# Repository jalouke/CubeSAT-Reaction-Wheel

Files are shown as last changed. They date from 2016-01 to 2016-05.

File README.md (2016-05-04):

# CubeSAT-Reaction-Wheel

Portland State University is developing Oregon’s first orbital satellite, a 2U Cubesat dubbed Oresat. This cubesat will use a reaction wheel system for attitude control and pointing of the onboard antennas and cameras. I am developing the controller, designing the structure and sourcing hardware for both the space rated system and a ground test system that will also be used for demonstration purposes. This system has been tested using the Dryden Drop Tower at PSU as well as in captive hanging tests. The current controller is a simple proportional controller, however using data collected from the drop test I will refine the model and implement a more sophisticated controller. Video of the tests can be seen at:  [Captive Controller Hanging Test](https://www.youtube.com/watch?v=Is1gPHlewtgand) and [Dryden Drop Tower Micro-Gravity Test](https://www.youtube.com/watch?v=cC2FpmCP5B4)

Both of the previous tests were conducted using a simple open loop proportional controller that was tuned via test to induce a slightly underdamped response. This was to create data that can be more easily compared to an ideal model.

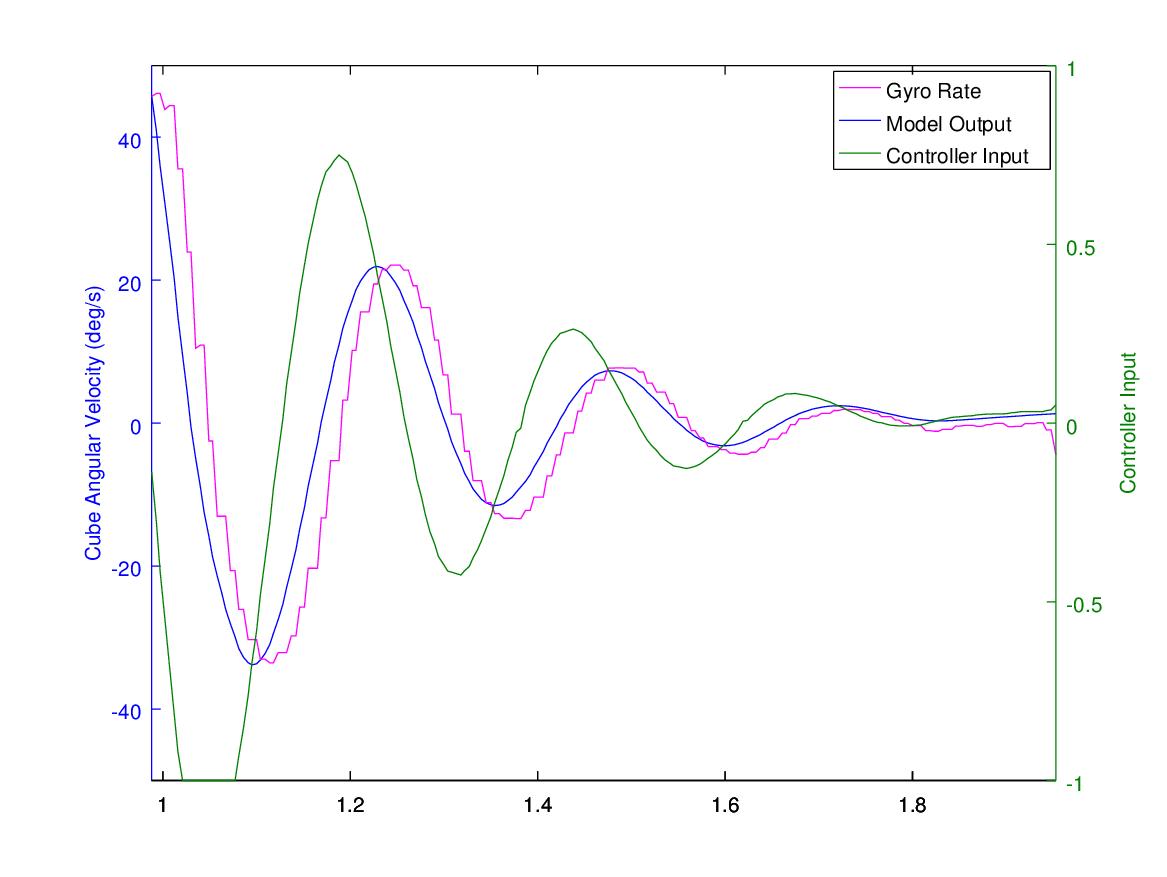
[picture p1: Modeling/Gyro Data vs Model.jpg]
CubeSat Model Comparison


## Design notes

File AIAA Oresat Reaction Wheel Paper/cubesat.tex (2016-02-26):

% `template.tex', a bare-bones example employing the AIAA class.
%
% For a more advanced example that makes use of several third-party
% LaTeX packages, see `advanced_example.tex', but please read the
% Known Problems section of the users manual first.
%
% Typical processing for PostScript (PS) output:
%
%  latex template
%  latex template   (repeat as needed to resolve references)
%
%  xdvi template    (onscreen draft display)
%  dvips template   (postscript)
%  gv template.ps   (onscreen display)
%  lpr template.ps  (hardcopy)
%
% With the above, only Encapsulated PostScript (EPS) images can be used.
%
% Typical processing for Portable Document Format (PDF) output:
%
%  pdflatex template
%  pdflatex template      (repeat as needed to resolve references)
%
%  acroread template.pdf  (onscreen display)
%
% If you have EPS figures, you will need to use the epstopdf script
% to convert them to PDF because PDF is a limmited subset of EPS.
% pdflatex accepts a variety of other image formats such as JPG, TIF,
% PNG, and so forth -- check the documentation for your version.
%
% If you do *not* specify suffixes when using the graphicx package's
% \includegraphics command, latex and pdflatex will automatically select
% the appropriate figure format from those available.  This allows you
% to produce PS and PDF output from the same LaTeX source file.
%
% To generate a large format (e.g., 11"x17") PostScript copy for editing
% purposes, use
%
%  dvips -x 1467 -O -0.65in,0.85in -t tabloid template
%
% For further details and support, read the Users Manual, aiaa.pdf.

% Try to reduce the number of latex support calls from people who
% don't read the included documentation.
%
\typeout{}\typeout{If latex fails to find aiaa-tc, read the README file!}
%

\documentclass[]{aiaa-tc}% insert '[draft]' option to show overfull boxes
\usepackage{amssymb}
\usepackage{amsmath} 

 \title{An Open-Source Reaction Wheel System for Oregon's First Satellite}

 \author{
  Jeremy A. Louke\\
  {\normalsize\itshape
   Portland State Aerospace Society, Portland, OR, 97201}\\
  \and
  Erin S. Schmidt\\
  {\normalsize\itshape
  Portland State University, Portland, OR, 97201}
 }

 % Data used by 'handcarry' option if invoked
 \AIAApapernumber{YEAR-NUMBER}
 \AIAAconference{Conference Name, Date, and Location}
 \AIAAcopyright{\AIAAcopyrightD{YEAR}}

 % Define commands to assure consistent treatment throughout document
 \newcommand{\eqnref}[1]{(\ref{#1})}
 \newcommand{\class}[1]{\texttt{#1}}
 \newcommand{\package}[1]{\texttt{#1}}
 \newcommand{\file}[1]{\texttt{#1}}
 \newcommand{\BibTeX}{\textsc{Bib}\TeX}

\begin{document}

\maketitle

\begin{abstract}
Portland State University is developing Oregon's first orbital satellite, a 2U Cubesat, dubbed Oresat. This cubesat will use a reaction wheel system for attitude control and pointing of the onboard low-gain antenna. Details of the current stage of development of the reaction wheel ground test article, and its controller, are presented here. Future work includes attitude control testing in the brief (2.1 s) free-fall environment of Portland State University's Dryden Drop Tower.
\end{abstract}

\section*{Nomenclature}

\begin{tabbing}
  XXX \= \kill% this line sets tab stop
  $M_0^{+ \circlearrowleft}$ \qquad Moment in the x-axis (N m)\\
  $T^0$ \qquad Torque (N m)\\
  $\theta$ \qquad Angular position (${}^{\circ}$)\\
  $\dot{\theta}$ \qquad Angular velocity(${}^{\circ}/s$)\\ 
  $\ddot{\theta}$ \qquad Angular velocity(${}^{\circ}/s^2$) \\
  $I$ \qquad Moment of Inertia (N $\textrm{m}^2$)\\
  $b$ \qquad Damping Coefficient (N s/m)\\ 
  $G$ \qquad Spring Coefficient (N/m)\\ \\
  \textit{Subscripts}\\
  $x$ \qquad Index for Cartesian axes \\
  $rw$\qquad Reaction Wheel\\
  $n$ \qquad Motor Index\\
  $A, B, C, D$ \qquad Indices for Motors A, B, C, and D\\
 \end{tabbing}

\section{Introduction}
Small educational satellites have been launched by dozens of universities around the United States as part of NASA’s CubeSat Launch Initiative, especially under the auspices of the Educational Launch of Nanosatellites (ELaNa) program. As of 2015 cubesats from 29 states have flown under the program, however the great state of Oregon has yet to join their ranks\cite{Mahoney:15bk}. During the summer of 2015 the Oresat project was initiated by the Portland State Aerospace Society to rectify this situation. The Portland State Aerospace Society (PSAS) is an engineering student organization and citizen science project located at Portland State University dedicated to developing low-cost, open-source, and open-hardware high-powered rockets and avionics systems with special interests in venture class launch vehicle technologies and nanosatellites\cite{PSAS:15bk}.\\

The Oresat satellite will be a Cal Poly design-specification 2U cubesat\cite{Cubesat:14bk}. Oresat is pictured in Figure \ref{fig:oresat}. The project objectives are to test several subsystems in the environment of a 400 km circular Low Earth Orbit, including PSAS’s Sputnik board, and DxWiFi subsystems. The Sputnik command, control, and communication (C3) board is based on a MKW01Z128 microcontroller, and has a custom “arduino-like” breakout. Sputnik is being designed expressly for the space environment, and will include some measure of fault-tolerance and radiation hardening. Another major project, dubbed DxWiFi, is to be able to communicate space-to-ground, and ground-to-space via a COTS IEEE 802.11b radio module aboard the cubesat. Ground stations for cubesat telemetry downlink are expected to be part of the SatNOGs open-source satellite ground station network. Due to practical issues with telemetry downlink power budgets and and the limitations of the low-gain deployable antenna some element of directional pointing is required. Following from this is the need for a robust system to provide attitude control for Oresat attitude control system. PSAS has selected a reaction wheel based system to provide attitude control for Oresat. Per PSAS’s open-source mandate all  (non-ITAR) project development deliverables are being made publicly available under a GNU GPL v2 license\cite{Oresat:15bk}. It is hoped by the authors, and the members of PSAS that the discourse around educational cubesats and their design will be elevated by making the information for this project publicly available.

\begin{figure}[h!]
  \centering
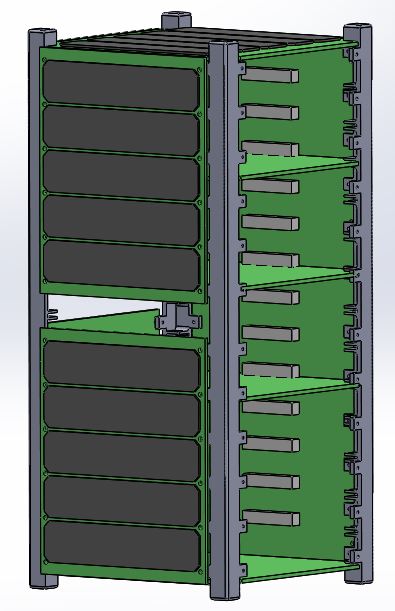
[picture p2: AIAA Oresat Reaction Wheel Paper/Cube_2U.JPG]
  
  \caption{Speculative mockup in SolidWorks of the Oresat chassis.}
  \label{fig:oresat}
\end{figure}

\section{Concept Definition}
	Angular rate and pointing precision requirements for the flight attitude control system are determined from orbital parameters (likely those offered by Nanoracks deployment from the ISS) and the expected performance of the PSAS DxWiFi telemetry system. The ground test article is a proof of concept and uses inexpensive COTS DC brushless motors which are significantly more powerful than those required for the flight use case. The ground test article is broadly similar in design to the flight system, for example by using 4 momentum-wheels in a pyramid configuration for added redundancy and on-orbit mission assurance. Such a design is similar one recently developed for a master's thesis project at California Polytechnic State University San Luis Obispo\cite{Logan:08bk}. A magnetorquer is used to periodically dump accumulated momentum into the Earth's magnetic field. The principle difference between the ground test and flight designs is that the ground test article uses the 1U form factor whereas Oresat will be 2U.

\section{Design and Fabrication}
	The Oresat reaction wheel system chassis was developed using rapid prototyping techniques over a short time period. This enables rapid design iteration cycles. A mockup 1U cubesat structure was drafted in SolidWorks CAD, and fabricated by FDM 3D printers. The cubesat structural rails were printed with recesses for hex nuts to ease assembly. The ground test article is shown in Figure \ref{fig:rcs} As previously noted there are several departures in the design of the ground test article from the flight system. Among these are COTS DC brushless motors used to drive the momentum wheels. Having a very high RPM limit, specifically 22,000 RPM, these motors provide substantially more torque, shaft power, and shaft speed than required by the flight system. The use of such motors is justified due to the need to counter 1-g gravity in benchtop tests, to react quickly to perturbations, and to test the limits of the controller rise time. Additionally, the ground test article is not constrained by requirements for power consumption as the flight system surely will be. 

\begin{figure}[h!]
  \centering
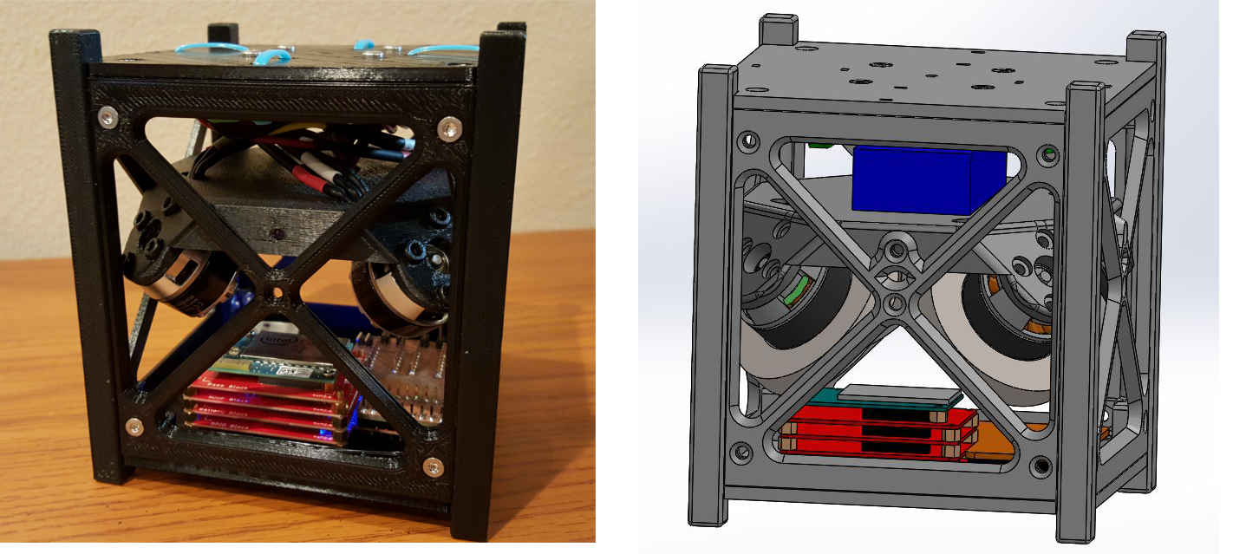
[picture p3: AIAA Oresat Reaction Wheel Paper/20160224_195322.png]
  
  \caption{Reaction wheel ground test articles, completed prototype and CAD design in SolidWorks.}
  \label{fig:rcs}
\end{figure}

\section{Controls Simulation and Design}
The Controller is implemented on an Intel Edison with code written in Python. The Edison receives feedback from a 9-DoF IMU and sends signals via GPIO to the motors. The top-level controller design procedure was as follows:
\begin{enumerate}
\item Determine the transfer functions from dynamics analysis of free body diagrams of the system
\item Create simulation in GNU Octave
\item Design the controller using classical Bode techniques
\end{enumerate}
The transfer functions are determined with a dynamics analysis of the free body diagram, shown schematically for a single axis in Figure \ref{fig:FBD}. The forces acting on the cube are the torques created by the motors $T_i^0$, damping effects $b_1 \dot{\theta}_{cube}$, and spring effects $G_1 \theta_{cube}$. Summing the moments around the center of gravity gives the following equation:\\

\begin{equation}
\label{eq:moment}
\sum M_0^{+ \circlearrowleft} = I_{x,cube} \ddot{\theta}_{x,cube} = T^0_{Ax} + T^0_{Bx} - T^0_{Cx} - T^0_{Dx} + T^0_x - \dot{\theta}_{x,cube} - G_x \theta_{x,cube}
\end{equation}\\
	
Solving Eqn. \ref{eq:moment} so that $\theta_{cube}$ and its derivatives are on the left side, and the motor torques are on the right side, as well as setting the system to Standard Equilibrium Position (at SEP the input perturbations are set to zero) and substituting the torque-inertia relation:\\

\[
T^0_x = 0
\]
\[
T^0_{nx} = I_{rw}\ddot{\theta}_n\]\\

This gives us the following equation:\\
 
\[
I_{x,cube} \alpha_x + b_x \dot{\theta}_{x,cube} + G_x \theta_{x,cube} = \sin(45^{\circ}) I_{rw} (\ddot{\theta}_A + \ddot{\theta}_B -\ddot{\theta}_C - \ddot{\theta}_D)
\]\\	
The definition of a transfer function is the output of a system with respect to a single input, so all motors are set to zero except for one (A for this example) and apply a Laplace transform to the equation:\\

\[
\frac{I_{x,cube}}{\sin(45^{\circ}) I_{rw}} \theta_{x,cube} s^2 +
\frac{b_x}{\sin(45^{\circ}) I_{rw}} \theta_{x,cube} s +
\frac{G_x}{\sin(45^{\circ}) I_{rw}} \theta_{x,cube} = \theta_A s^2
\]\\
	
Finally moving $\theta_{cube}$ and $\theta_A$ to the left side of the equation and everything else to the right, gives us a transfer function:\\

\begin{equation}
\label{eq:xfer}
G_A(s)=\frac{\theta_{x,cube}(s)}{\theta_A(s)}=\frac{s^2}{\cfrac{I_{x,cube}}{\sin(45^{\circ}) I_{rw}}s^2 + \cfrac{b_x}{\sin(45^{\circ}) I_{rw}}s + \cfrac{G_x}{\sin(45^{\circ}) I_{rw}}}
\end{equation}\\
	
Using the transfer functions, given schematically for one axis by Eqn. \ref{eq:xfer} a simulation was created in GNU Octave which yielded step response plots shown in Figure \ref{fig:simulation}. The simulation will further aid in Bode analysis for the determination of stability margins. These relate the frequency response of the system to its time response. The Margins can be adjusted with the use of a controller to affect the time response characteristics of the system. In the case of the ground test system the rise time for a $90^{\circ}$ step input should be under 1 second. 
\begin{figure}[h!]
  \centering
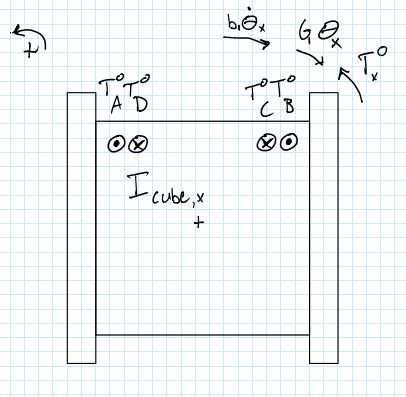
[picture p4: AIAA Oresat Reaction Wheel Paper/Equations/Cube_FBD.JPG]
  
  \caption{Free Body Diagram of the cubesat in the Cartesian X axis.}
  \label{fig:FBD}
\end{figure}

\begin{figure}[h!]
  \centering
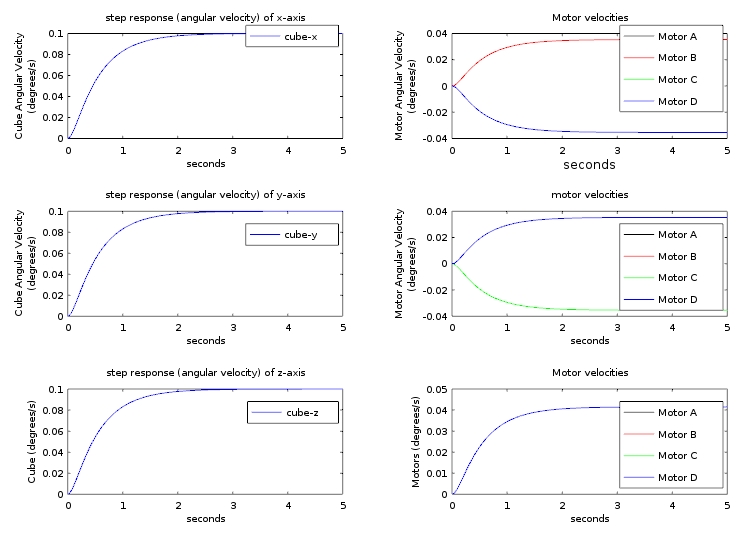
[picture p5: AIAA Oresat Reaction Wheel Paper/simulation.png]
  
  \caption{Angular velocity step responses in the cardinal axes of the CubeSat (left side), and individual motor velocities (right side).}
  \label{fig:simulation}
\end{figure}
\section{Future work}
An exciting testing opportunity involves exploiting the high-quality $\mu$-gravity environment of Portland State University's Dryden Drop Tower (DDT) facility for free fall tests of the reaction wheel system. The Dryden Drop Tower, patterned on the 2.2 Second Drop Tower facility at NASA's Glenn Research Center in Cleveland, Ohio, is optimized for exceptionally fast drop turnaround times. The DDT is one of the most productive Drop Towers in the world for its class, with more than xx drops over its xx year history. The DDT's 2.1 seconds of free-fall conditions provide unique opportunities for the observation of phenomena that are usually masked at the macro-scale in 1-g gravity fields. In the planned experiment the reaction wheel system will be commanded to complete two independent $90^{\circ}$ roll programs of the cubesat in the brief cinderella-like moment before the simulacrum of $\mu$-gravity disappears 2.1 seconds later.

It is expected that the 1-g and $\mu$-gravity testing campaigns for the Oresat reaction wheel system will be completed by early June. This should leave a substantial allowance of time for further design iterations leading up to the Oresat Critical Design Review before the next round of ELaNa proposals are due in November 2016.

\begin{thebibliography}{9}% maximum number of references (for label width)

\bibitem{Mahoney:15bk}
Mahoney, Erin. {\it CubeSat Launch Initiative: 50 CubeSats from 50 States in 5 Years.} NASA, April 9, 2015. http://www.nasa.gov/content/cubesat-launch-initiative-50-cubesats-from-50-states-in-5-years.\\

\bibitem{PSAS:15bk}
{\it Portland State Aerospace.} PSAS. Accessed February 25, 2016. http://psas.pdx.edu.\\

\bibitem{Cubesat:14bk}
The CubeSat Program, {\it Cal Poly SLO. CubeSat Design Specification Rev. 13.} San Luis
Obispo: California Polytechnic State University; 2014.\\

\bibitem{Oresat:15bk}
{\it Oregon Small Satellite Project.} GitHub. Accessed February 25, 2016. https://github.com/oresat.\\

\bibitem{Logan:08bk}
Logan, Jeffery. {\it Control and Sensor Development on a Four-Wheel Pyramidal Reaction Wheel Platform,} Master’s Thesis, California Polytechnic State University, San Luis Obispo, 2008.\\

\end{thebibliography}

\end{document}

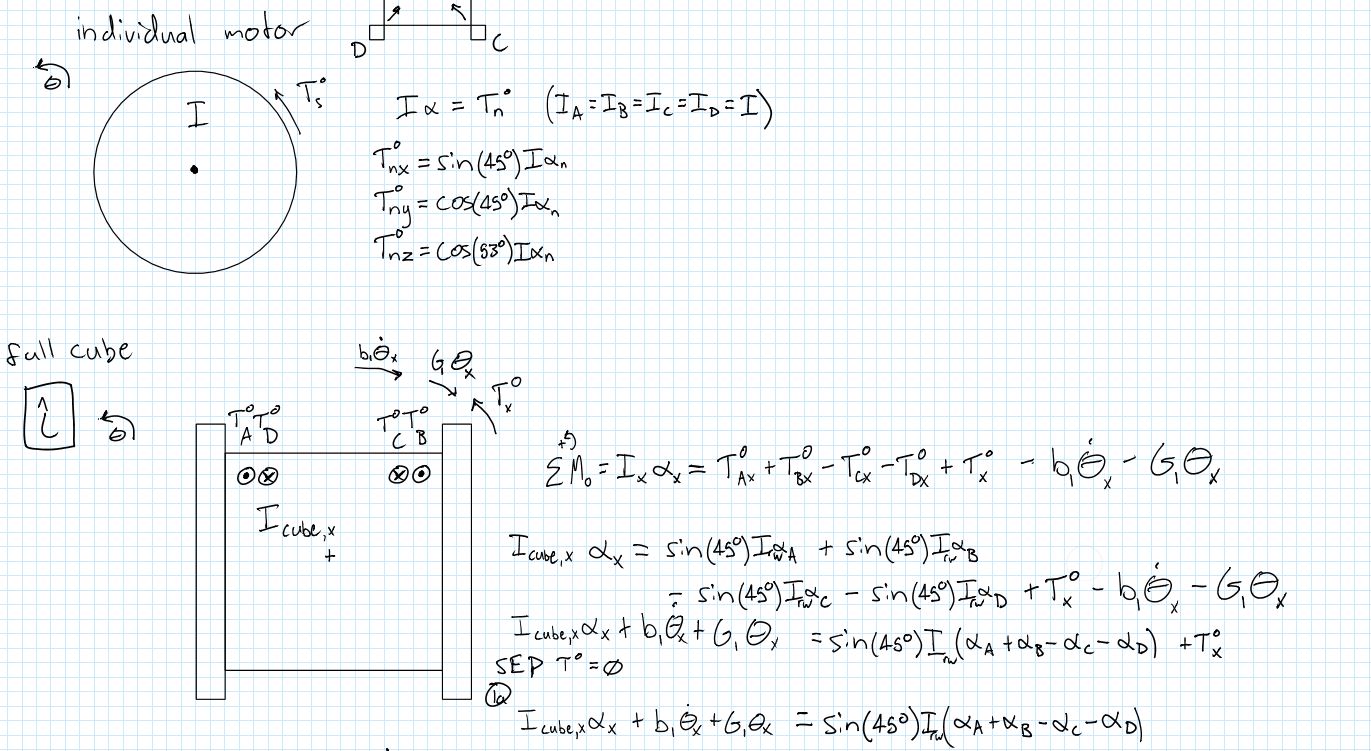
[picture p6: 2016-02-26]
AIAA Oresat Reaction Wheel Paper/Equations/Moment Sum and equation 1_a.JPG

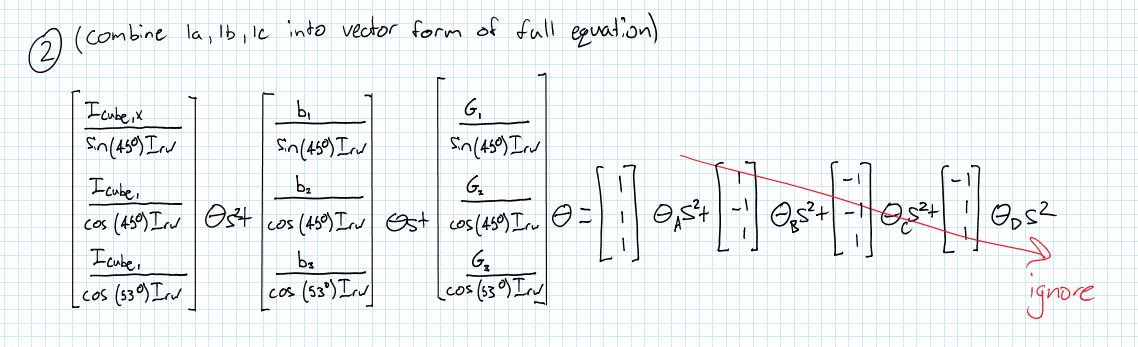
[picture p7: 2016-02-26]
AIAA Oresat Reaction Wheel Paper/Equations/Equation 2.JPG

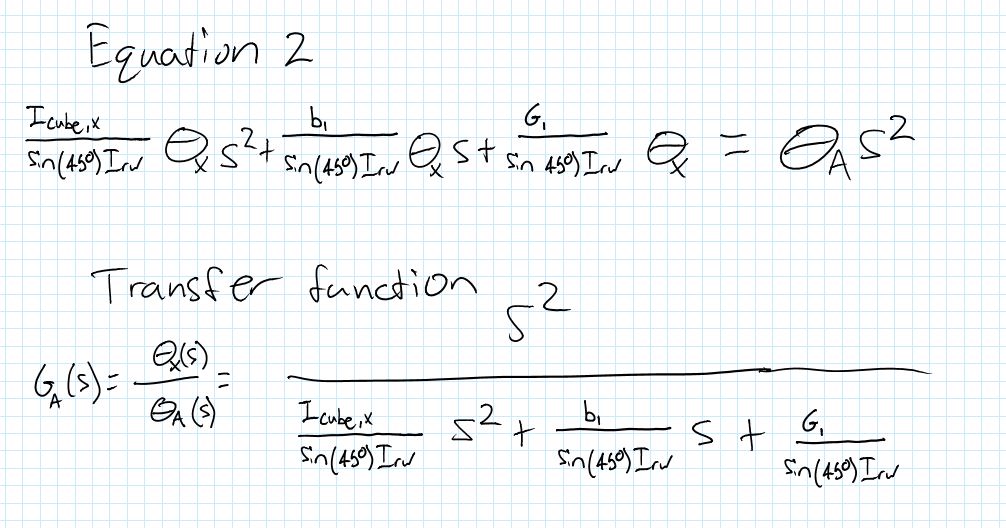
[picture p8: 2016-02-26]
AIAA Oresat Reaction Wheel Paper/Equations/CubeSat Transfer function and Equation 2.JPG

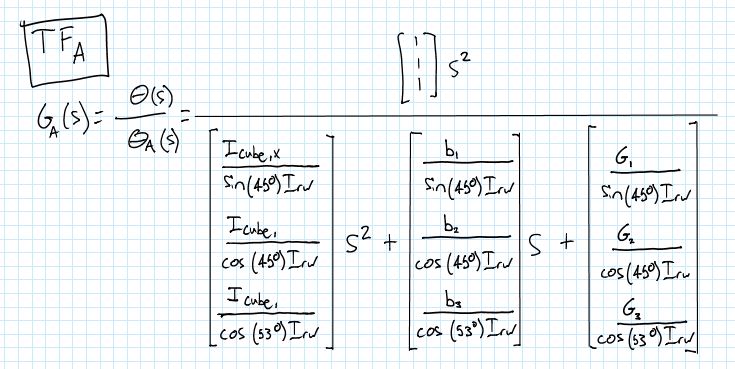
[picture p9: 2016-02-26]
AIAA Oresat Reaction Wheel Paper/Equations/Transfer Function.JPG

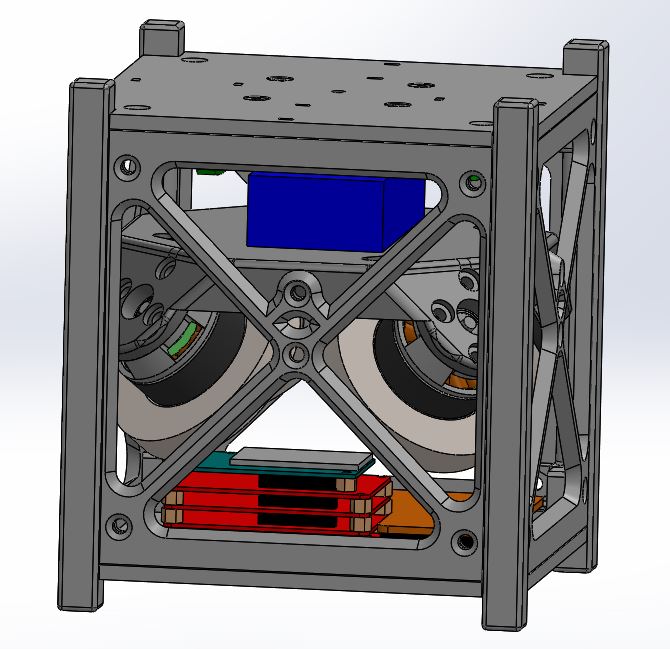
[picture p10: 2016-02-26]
AIAA Oresat Reaction Wheel Paper/Cube_RW_Full.JPG

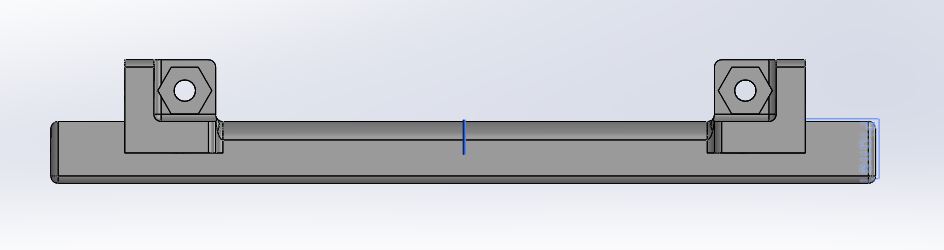
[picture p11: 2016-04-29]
SW_CAD_1U_cubesat/New STL/Corner rail.JPG

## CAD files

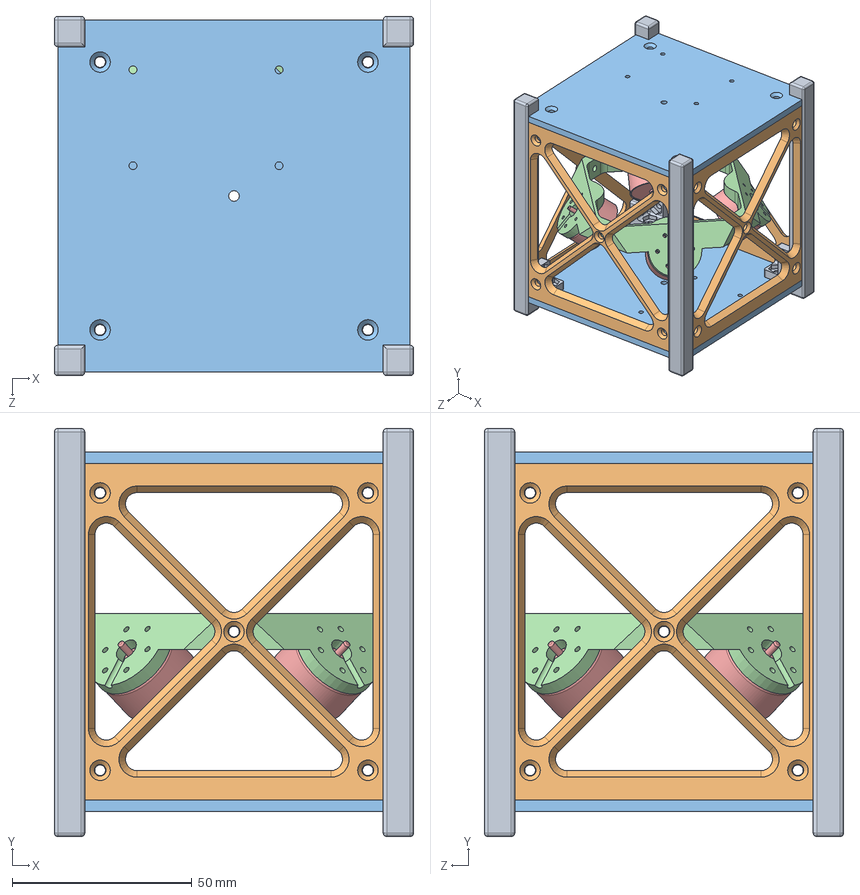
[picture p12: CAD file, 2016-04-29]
SW_CAD_1U_cubesat/V1/Cube sat assembly.SLDASM
100.0 x 113.5 x 100.0 mm
Corner rail x 4
Sides x 4
Z side x 2
reaction wheel mount
reaction wheel motor x 4

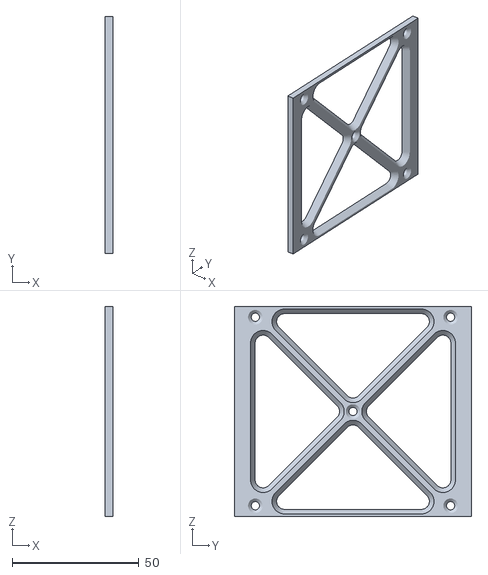
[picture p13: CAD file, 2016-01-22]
SW_CAD_1U_cubesat/V1/STL/Cube sat assembly - Sides-2.STL
3.17 x 93.6 x 83.0

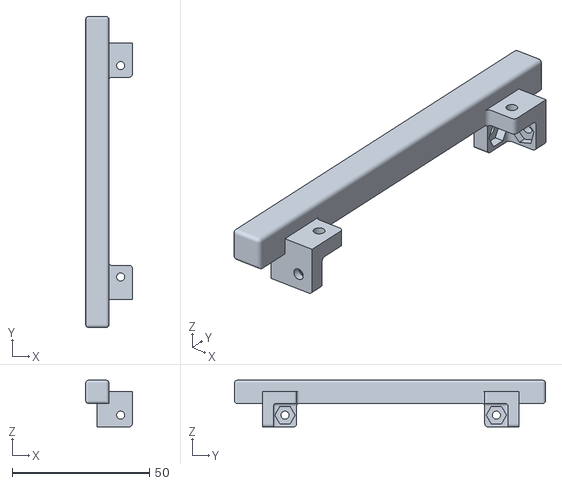
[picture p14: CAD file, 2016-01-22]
SW_CAD_1U_cubesat/V1/STL/Cube sat assembly - Corner rail-4.STL
17.0 x 113.5 x 17.0

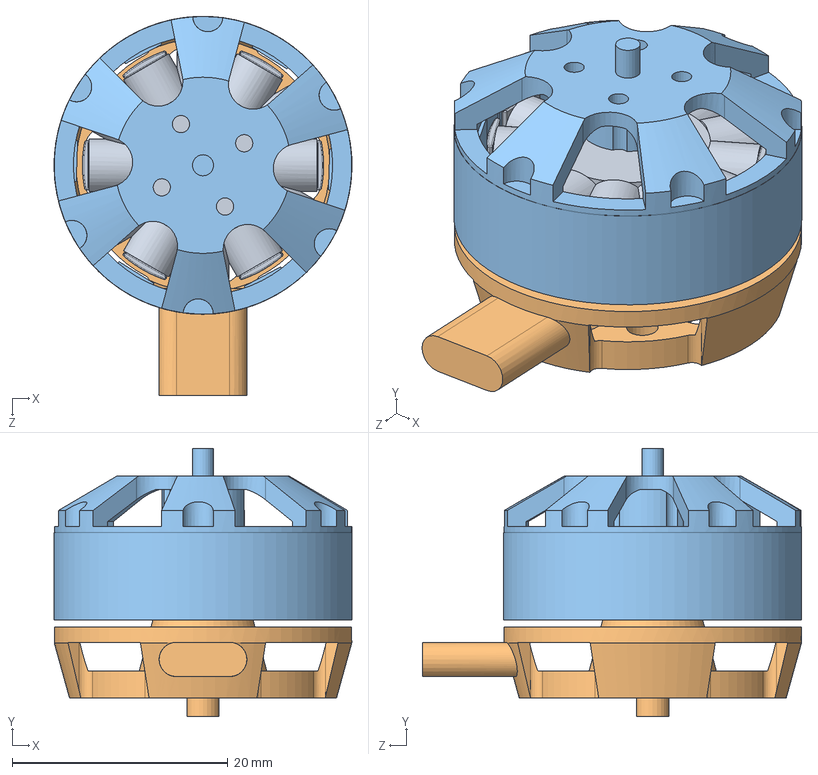
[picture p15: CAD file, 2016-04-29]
SW_CAD_1U_cubesat/Brushless Motor (Quantum MT2206)/Brushless Motor.SLDASM
27.6 x 24.8 x 35.1 mm
Brushless motor coil
Brushless motor bottom
Brushless motor top

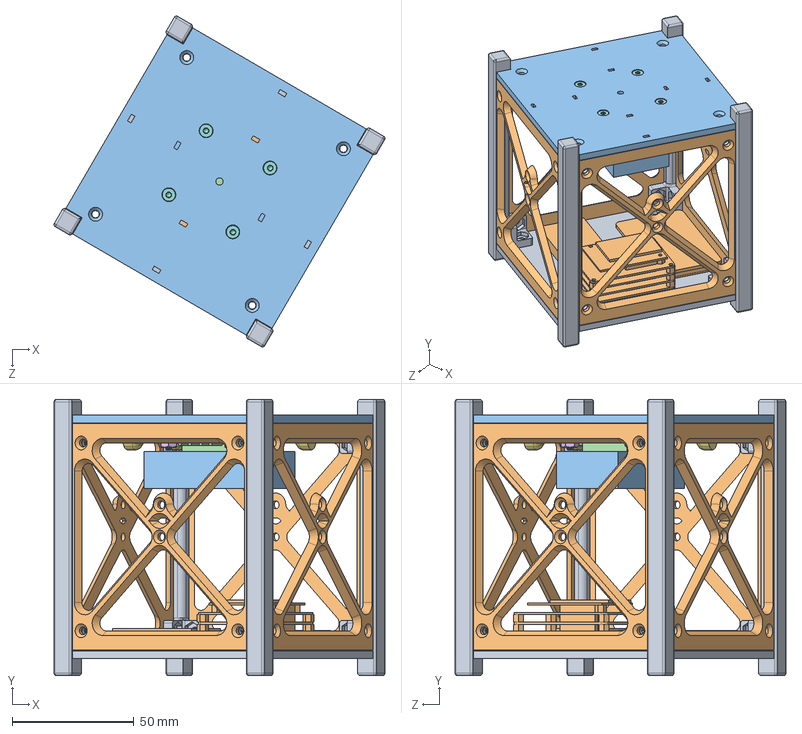
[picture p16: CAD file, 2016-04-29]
SW_CAD_1U_cubesat/Cube sat assembly (no motors).SLDASM
136.0 x 113.5 x 136.0 mm
Corner rail x 4
Sides x 4
Z side (top)
power distributer
4-40 .25in standoff x 4
4-40 hex nut x 4
ESC 10A x 4
4-40 .25 flat head screw x 4
Z side (bottom)
edison stack
e-flite 450mAh 3s LiPo

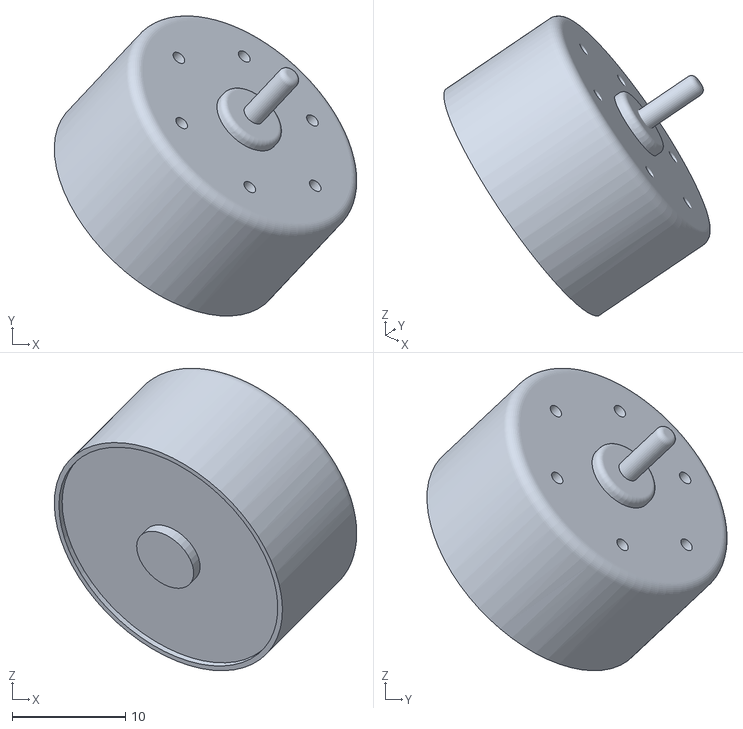
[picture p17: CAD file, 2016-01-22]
SW_CAD_1U_cubesat/V1/STL/Cube sat assembly - reaction wheel motor-1.STL
26.7 x 26.5 x 26.7

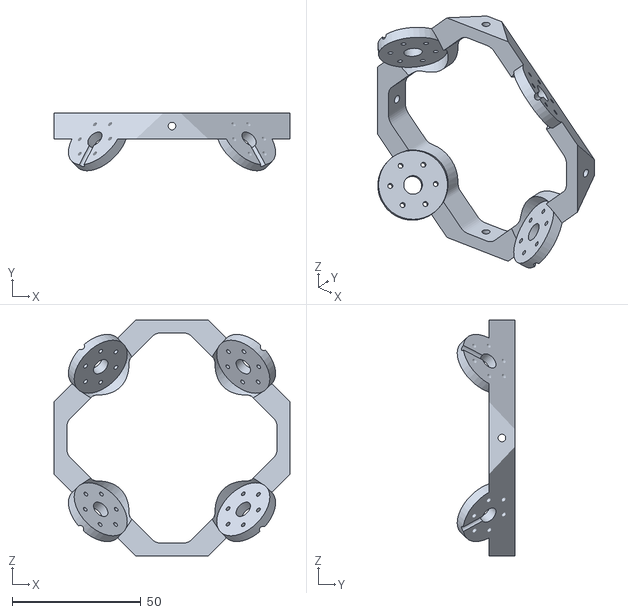
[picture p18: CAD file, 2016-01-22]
SW_CAD_1U_cubesat/V1/STL/Cube sat assembly - reaction wheel mount-1.STL
91.7 x 22.4 x 91.7

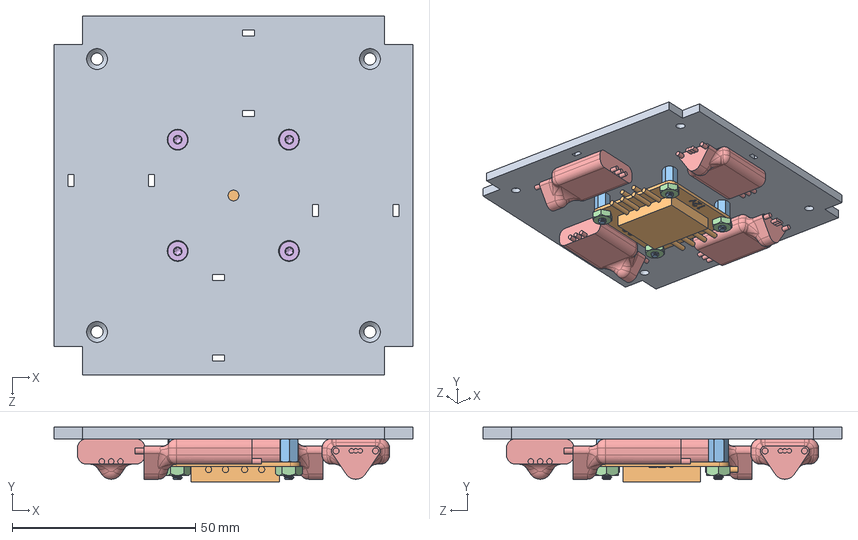
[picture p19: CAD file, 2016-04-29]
SW_CAD_1U_cubesat/Z side (top).SLDASM
98.0 x 14.9 x 98.0 mm
Z side (top)
power distributer
4-40 .25in standoff x 4
4-40 hex nut x 4
ESC 10A x 4
4-40 .25 flat head screw x 4

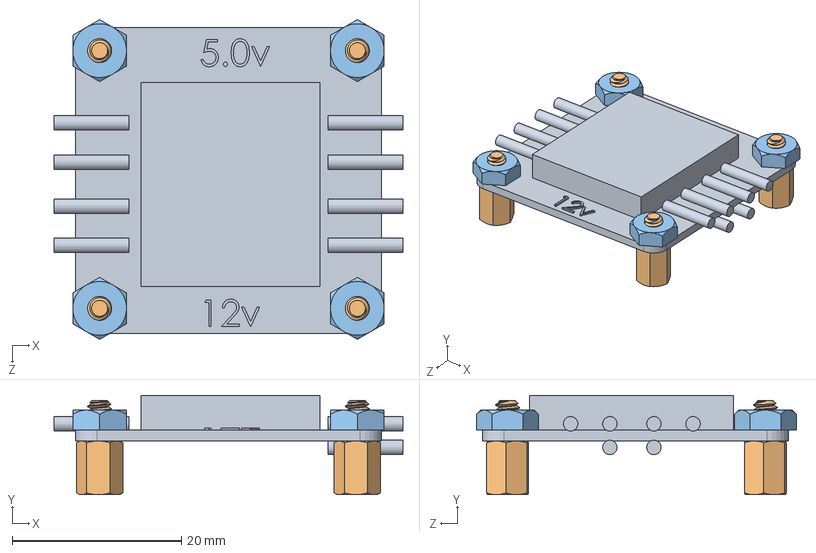
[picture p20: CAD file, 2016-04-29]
SW_CAD_1U_cubesat/distributor with standoffs.SLDASM
41.3 x 11.7 x 37.8 mm
power distributer
4-40 .25in standoff x 4
4-40 hex nut x 4

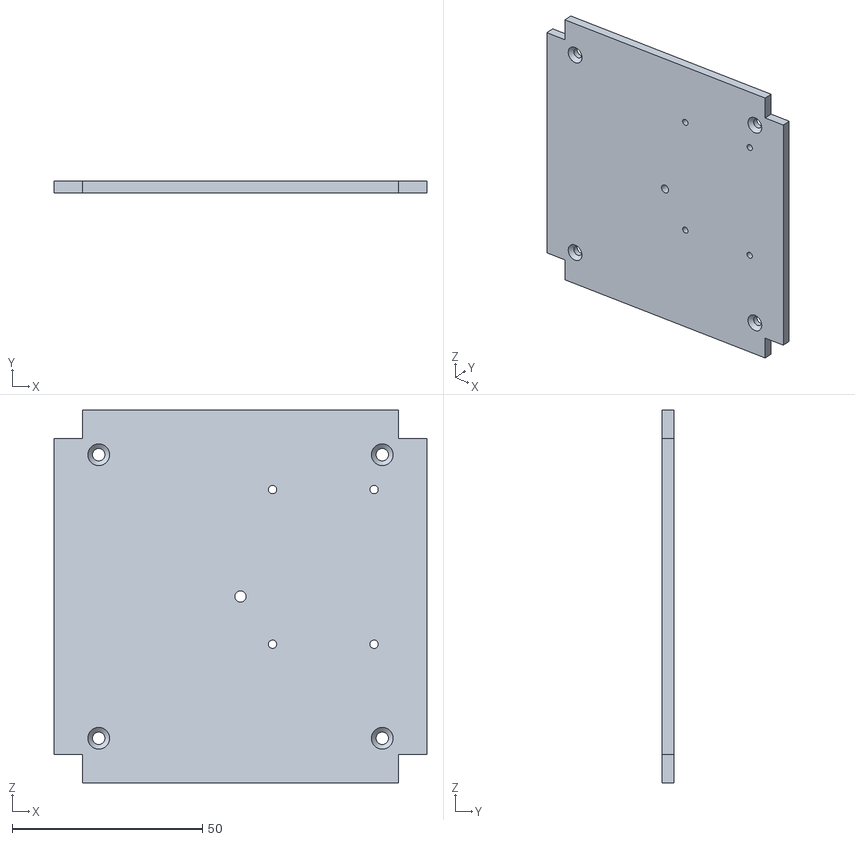
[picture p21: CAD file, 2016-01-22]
SW_CAD_1U_cubesat/V1/STL/Cube sat assembly - Z side-3.STL
98.0 x 3.18 x 98.0

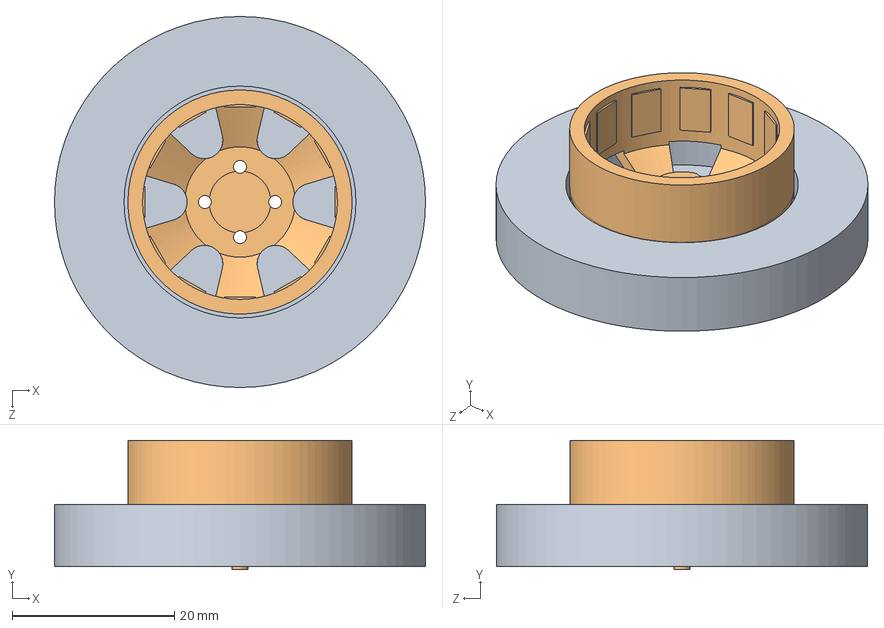
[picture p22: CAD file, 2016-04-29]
SW_CAD_1U_cubesat/Motor rotational inertia.SLDASM
45.7 x 15.9 x 45.7 mm
extra mass
Brushless motor top

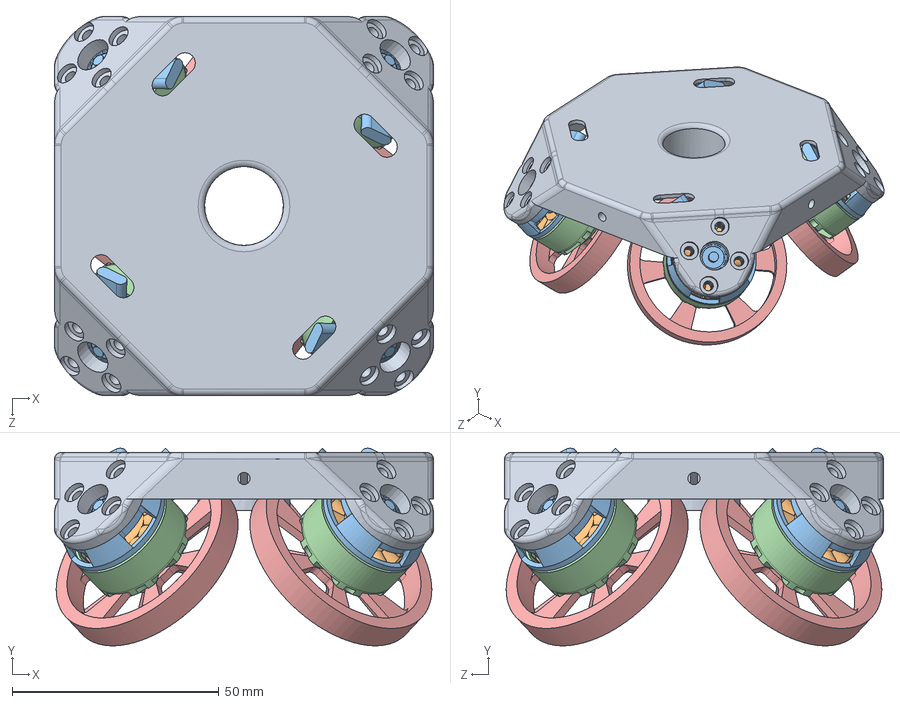
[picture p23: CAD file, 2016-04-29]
SW_CAD_1U_cubesat/motors on mount.SLDASM
91.7 x 47.8 x 91.7 mm
reaction wheel mount
Brushless motor coil x 4
Brushless motor bottom x 4
Brushless motor top x 4
extra mass x 4

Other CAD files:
SW_CAD_1U_cubesat/V1/STL/Cube sat assembly - Sides-3.STL
SW_CAD_1U_cubesat/V1/STL/Cube sat assembly - Corner rail-3.STL
SW_CAD_1U_cubesat/V1/STL/Cube sat assembly - Corner rail-1.STL
SW_CAD_1U_cubesat/V1/STL/Cube sat assembly - Sides-4.STL
SW_CAD_1U_cubesat/V1/STL/Cube sat assembly - reaction wheel motor-4.STL
SW_CAD_1U_cubesat/V1/STL/Cube sat assembly - Sides-1.STL
SW_CAD_1U_cubesat/Brushless Motor (Quantum MT2206)/Brushless motor bottom.SLDPRT
SW_CAD_1U_cubesat/Brushless Motor (Quantum MT2206)/Brushless motor coil.SLDPRT
SW_CAD_1U_cubesat/Brushless Motor (Quantum MT2206)/Brushless motor top.SLDPRT
SW_CAD_1U_cubesat/Brushless motor.SLDPRT
SW_CAD_1U_cubesat/Corner rail.SLDPRT
SW_CAD_1U_cubesat/Cube sat assembly.SLDASM
SW_CAD_1U_cubesat/ESC 10A.SLDPRT
SW_CAD_1U_cubesat/Hardware/4-40 .25 button head screw.SLDPRT
SW_CAD_1U_cubesat/Hardware/4-40 .25 flat head screw.SLDPRT
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

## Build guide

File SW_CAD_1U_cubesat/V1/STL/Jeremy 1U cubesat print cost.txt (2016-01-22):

4x corner rails - Mojo, 2.8+.6 in^3

	$27.20

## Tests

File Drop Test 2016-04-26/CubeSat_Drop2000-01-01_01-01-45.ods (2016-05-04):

Time | ACCx | ACCy | ACCz | GYRx | GYRy | GYRz | MAGx | MAGy | MAGz | Motor_Speed
66.329 | -0.051 | 0.006 | -0.272 | 0.664 | 0.937 | -0.41 | -108.378 | 372.705 | -679.334
66.333 | -0.078 | 0.017 | -0.04 | 0.664 | 0.937 | -0.41 | -108.378 | 372.705 | -679.334
66.338 | -0.078 | 0.017 | -0.04 | 0.664 | 0.937 | -0.156 | -108.378 | 372.705 | -679.334
66.343 | -0.078 | 0.003 | -0.037 | -1.138 | 1.042 | -0.156 | -108.378 | 372.705 | -679.334
66.347 | -0.118 | 0.003 | -0.037 | -1.138 | 1.042 | -0.156 | -108.378 | 381.674 | -675.14
66.352 | -0.118 | 0.003 | -0.037 | -1.269 | 0.517 | 7.807 | -90.1 | 381.674 | -675.14
66.356 | -0.107 | 0.008 | -0.041 | -1.269 | 0.517 | 7.807 | -90.1 | 381.674 | -675.14
66.361 | -0.107 | 0.008 | -0.041 | -1.086 | 0.211 | 16.181 | -90.1 | 381.674 | -675.14
66.366 | -0.086 | 0.009 | -0.038 | -1.086 | 0.211 | 16.181 | -90.1 | 381.674 | -675.14
66.37 | -0.086 | 0.009 | -0.038 | -1.086 | 0.211 | 16.181 | -94.669 | 367.429 | -629.853
66.375 | -0.095 | -0.001 | -0.048 | -1.514 | 0.675 | 22.717 | -94.669 | 367.429 | -629.853
66.379 | -0.095 | -0.001 | -0.048 | -1.514 | 0.675 | 22.717 | -94.669 | 367.429 | -629.853
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

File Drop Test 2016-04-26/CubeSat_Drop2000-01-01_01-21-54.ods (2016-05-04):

Time | ACCx | ACCy | ACCz | GYRx | GYRy | GYRz | MAGx | MAGy | MAGz | Motor_Speed
219.943 | -0.067 | 0.011 | -0.041 | 0.061 | 0.395 | 2.146 | -68.267 | 414.383 | -655.432
219.948 | -0.11 | 0.001 | -0.051 | -0.053 | 0.325 | 1.244 | -68.267 | 414.383 | -655.432
219.953 | -0.11 | 0.001 | -0.051 | -0.132 | 0.5 | 9.198 | -68.267 | 414.383 | -655.432
219.957 | -0.102 | 0.009 | -0.056 | -0.132 | 0.5 | 9.198 | -68.267 | 414.383 | -655.432
219.962 | -0.102 | 0.009 | -0.056 | -0.132 | 0.5 | 9.198 | -126.657 | 392.753 | -583.308
219.966 | -0.087 | 0.013 | -0.041 | -0.263 | 0.605 | 17.292 | -126.657 | 392.753 | -583.308
219.971 | -0.087 | 0.013 | -0.041 | -0.263 | 0.605 | 17.292 | -126.657 | 392.753 | -583.308
219.975 | -0.087 | 0.013 | -0.041 | -0.569 | 0.491 | 23.793 | -126.657 | 392.753 | -583.308
219.98 | -0.089 | 0.01 | -0.031 | -0.569 | 0.491 | 23.793 | -126.657 | 392.753 | -583.308
219.985 | -0.089 | 0.01 | -0.031 | -0.569 | 0.491 | 28.518 | -159.153 | 400.139 | -536.343
219.989 | -0.076 | 0.01 | -0.042 | -1.033 | 0.263 | 28.518 | -159.153 | 400.139 | -536.343
219.994 | -0.076 | 0.01 | -0.042 | -1.033 | 0.263 | 28.518 | -159.153 | 400.139 | -536.343
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

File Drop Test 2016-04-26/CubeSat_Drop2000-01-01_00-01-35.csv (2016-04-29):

Time | ACCx | ACCy | ACCz | GYRx | GYRy | GYRz | MAGx | MAGy | MAGz | Motor_Speed
253.447 | -0.080 | 0.001 | -0.507 | 0.472 | 1.375 | -0.007 | -20.539 | 156.402 | -633.208
253.452 | -0.080 | 0.007 | -0.042 | 0.472 | 1.375 | -0.007 | -20.539 | 156.402 | -633.208
253.456 | -0.088 | 0.007 | -0.042 | -0.718 | 2.101 | 0.142 | -20.539 | 195.442 | -701.977
253.461 | -0.088 | 0.007 | -0.042 | -0.718 | 2.101 | 0.142 | 38.360 | 195.442 | -701.977
253.465 | -0.102 | 0.003 | -0.032 | -1.164 | 1.926 | 5.523 | 38.360 | 195.442 | -701.977
253.470 | -0.102 | 0.003 | -0.032 | -1.164 | 1.926 | 5.523 | 38.360 | 195.442 | -701.977
253.475 | -0.093 | 0.014 | -0.048 | -1.164 | 1.926 | 5.523 | 38.360 | 195.442 | -701.977
253.479 | -0.093 | 0.014 | -0.048 | -1.313 | 1.961 | 14.536 | 49.022 | 174.867 | -649.981
253.484 | -0.096 | 0.004 | -0.047 | -1.313 | 1.961 | 14.536 | 49.022 | 174.867 | -649.981
253.488 | -0.096 | 0.004 | -0.047 | -1.637 | 2.092 | 20.827 | 49.022 | 174.867 | -649.981
253.493 | -0.096 | 0.011 | -0.034 | -1.637 | 2.092 | 20.827 | 49.022 | 174.867 | -649.981
253.497 | -0.081 | 0.011 | -0.034 | -1.637 | 2.092 | 26.129 | 49.022 | 168.009 | -615.176
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

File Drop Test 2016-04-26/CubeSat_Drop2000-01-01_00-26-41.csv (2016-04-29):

Time | ACCx | ACCy | ACCz | GYRx | GYRy | GYRz | MAGx | MAGy | MAGz | Motor_Speed
491.891 | -0.056 | 0.012 | -0.294 | 1.076 | -0.489 | -0.208 | -318.077 | 284.601 | -571.986
491.896 | -0.056 | 0.012 | -0.107 | 2.624 | -1.277 | -0.287 | -318.077 | 284.601 | -571.986
491.900 | -0.085 | 0.017 | -0.056 | 2.624 | -1.277 | -0.287 | -318.077 | 284.601 | -571.986
491.905 | -0.085 | 0.017 | -0.056 | 2.624 | -1.277 | 3.476 | -317.569 | 309.397 | -666.754
491.909 | -0.092 | -0.004 | -0.051 | 1.741 | -2.038 | 3.476 | -317.569 | 309.397 | -666.754
491.914 | -0.092 | -0.004 | -0.051 | 1.741 | -2.038 | 3.476 | -317.569 | 309.397 | -666.754
491.919 | -0.107 | 0.012 | -0.030 | 1.513 | -2.029 | 12.007 | -317.569 | 309.397 | -666.754
491.923 | -0.107 | 0.012 | -0.030 | 1.513 | -2.029 | 12.007 | -293.197 | 291.460 | -636.143
491.928 | -0.107 | 0.007 | -0.036 | 1.268 | -1.653 | 19.453 | -293.197 | 291.460 | -636.143
491.932 | -0.090 | 0.007 | -0.036 | 1.268 | -1.653 | 19.453 | -293.197 | 291.460 | -636.143
491.937 | -0.090 | 0.007 | -0.036 | 1.268 | -1.653 | 19.453 | -293.197 | 291.460 | -636.143
491.942 | -0.090 | 0.018 | -0.055 | 0.909 | -1.574 | 24.808 | -293.197 | 291.460 | -636.143
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

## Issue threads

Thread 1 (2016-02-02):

GPIO 48 (edison, mraa 33) interferes with wifi

jalouke, 2016-02-02:
will need to hack the gpio to motor board. Change GP48 to GP46 (mraa 32), and make adjustment to code.

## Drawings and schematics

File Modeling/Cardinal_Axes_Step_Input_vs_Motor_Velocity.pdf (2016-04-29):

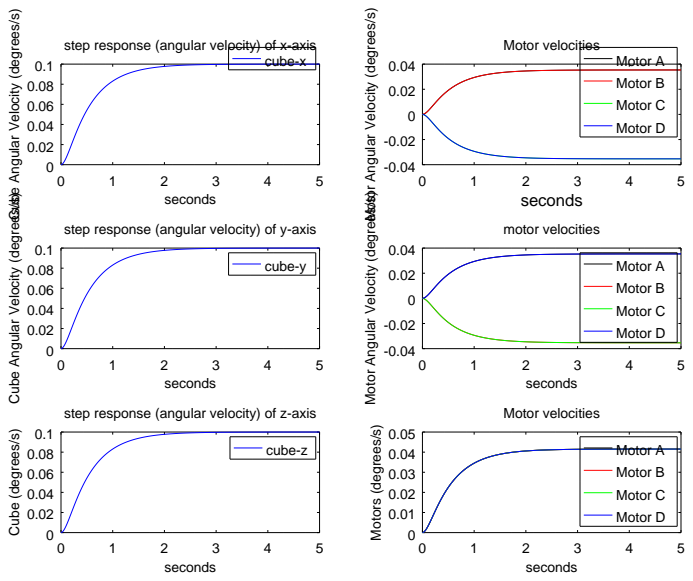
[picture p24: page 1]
seconds; (degrees/s); cube-x; Motor A Motor B Motor C Motor D; cube-y; Cube (degrees/s); cube-z; Motors (degrees/s); step response (angular velocity) of x-axis; Motor velocities; step response (angular velocity) of y-axis; motor velocities; step response (angular velocity) of z-axis

Cube Angular Velocity

Motor Angular Velocity

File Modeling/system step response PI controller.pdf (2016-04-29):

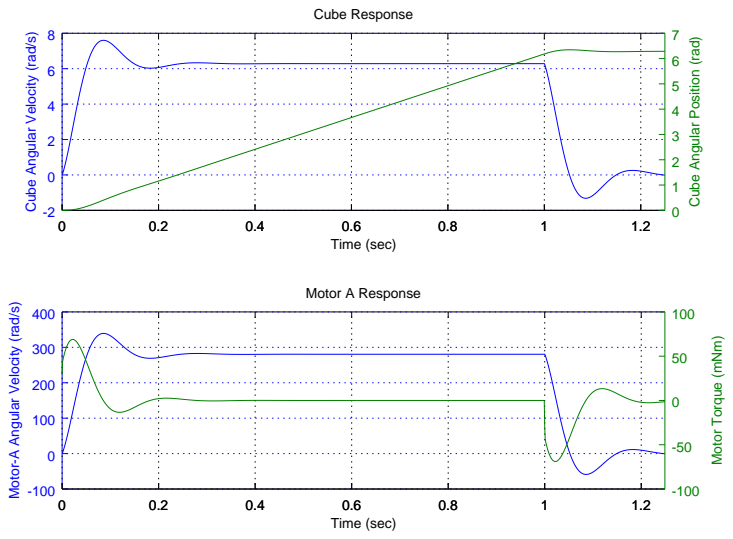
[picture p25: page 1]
Time (sec); Cube Response; Motor A Response

Cube Angular Velocity (rad/s)

Cube Angular Position (rad)

Motor-A Angular Velocity (rad/s)

Motor Torque (mNm)

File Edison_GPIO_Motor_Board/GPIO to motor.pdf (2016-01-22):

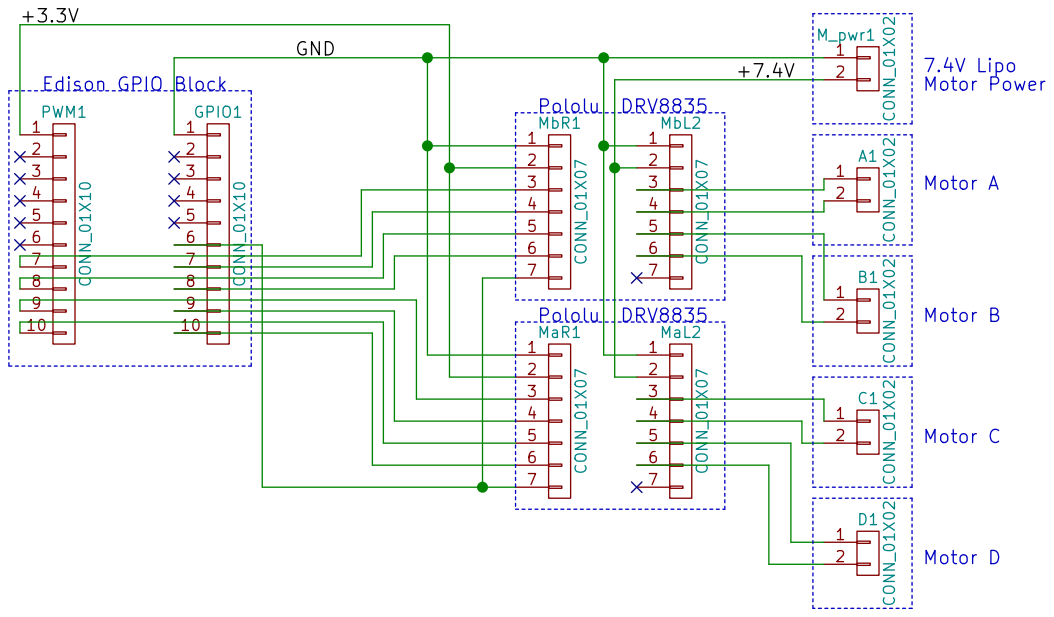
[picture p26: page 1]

Id: 1/1 Title: File: GPIO to motor.sch Sheet: / 123456789

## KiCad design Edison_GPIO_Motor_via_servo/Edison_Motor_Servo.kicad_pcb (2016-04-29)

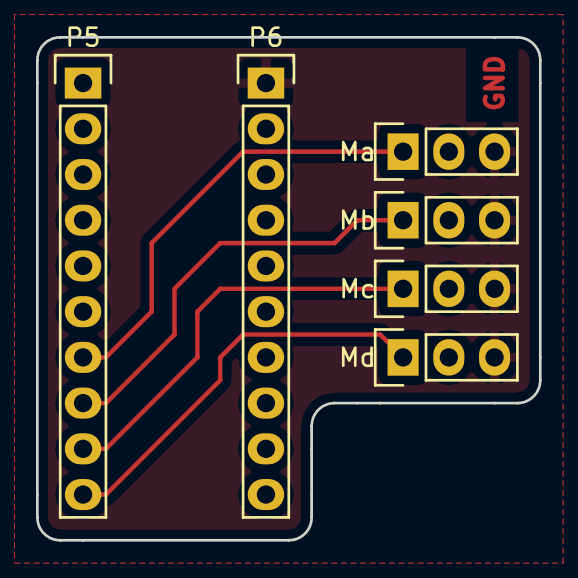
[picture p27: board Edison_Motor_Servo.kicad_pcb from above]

Board: 2 copper layers, 27.9 x 27.9 mm, 6 parts (0 on the bottom side), 5 nets.

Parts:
Ma: CONN_01X03; Socket_Strip_Straight_1x03
Mb: CONN_01X03; Socket_Strip_Straight_1x03
Mc: CONN_01X03; Socket_Strip_Straight_1x03
Md: CONN_01X03; Socket_Strip_Straight_1x03
P5, P6: CONN_01X10; Socket_Strip_Straight_1x10

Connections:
GND: Ma.3, Mb.3, Mc.3, Md.3, P6.1
unnamed: Ma.1, P5.7
unnamed: Mb.1, P5.8
unnamed: Mc.1, P5.9
unnamed: Md.1, P5.10

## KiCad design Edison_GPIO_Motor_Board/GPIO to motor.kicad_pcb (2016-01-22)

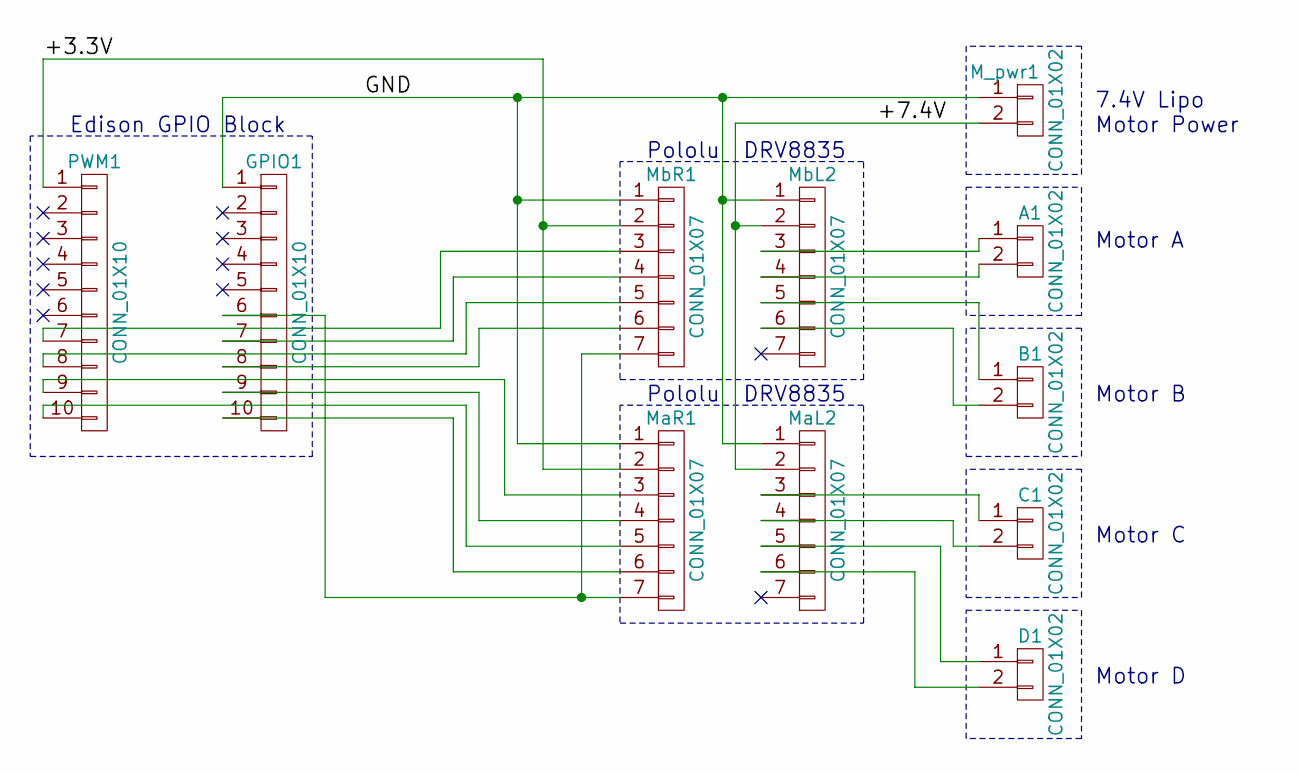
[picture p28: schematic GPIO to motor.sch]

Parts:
A1: CONN_01X02; Pin_Header_Straight_1x02
B1: CONN_01X02; Pin_Header_Straight_1x02
C1: CONN_01X02; Pin_Header_Straight_1x02
D1: CONN_01X02; Pin_Header_Straight_1x02
GPIO1: CONN_01X10; Pin_Header_Straight_1x10
M_pwr1: CONN_01X02; Pin_Header_Straight_1x02
MaL2: CONN_01X07; Pin_Header_Straight_1x07
MaR1: CONN_01X07; Pin_Header_Straight_1x07
MbL2: CONN_01X07; Pin_Header_Straight_1x07
MbR1: CONN_01X07; Pin_Header_Straight_1x07
PWM1: CONN_01X10; Pin_Header_Straight_1x10

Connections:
+3V3: MaR1.2, MbR1.2, PWM1.1
+BATT: M_pwr1.2, MaL2.2, MbL2.2
GND: GPIO1.1, M_pwr1.1, MaL2.1, MaR1.1, MbL2.1, MbR1.1
unnamed: A1.1, MbL2.3
unnamed: A1.2, MbL2.4
unnamed: B1.1, MbL2.5
unnamed: B1.2, MbL2.6
unnamed: C1.1, MaL2.3
unnamed: C1.2, MaL2.4
unnamed: D1.1, MaL2.5
unnamed: D1.2, MaL2.6
unnamed: GPIO1.6, MaR1.7, MbR1.7
unnamed: GPIO1.7, MbR1.4
unnamed: GPIO1.8, MbR1.6
unnamed: GPIO1.9, MaR1.4
unnamed: GPIO1.10, MaR1.6
unnamed: MaR1.3, PWM1.9
unnamed: MaR1.5, PWM1.10
unnamed: MbR1.3, PWM1.7
unnamed: MbR1.5, PWM1.8

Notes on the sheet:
Edison GPIO Block
Pololu DRV8835
Motor A
Motor B
Motor C
Motor D
7.4V Lipo Motor Power

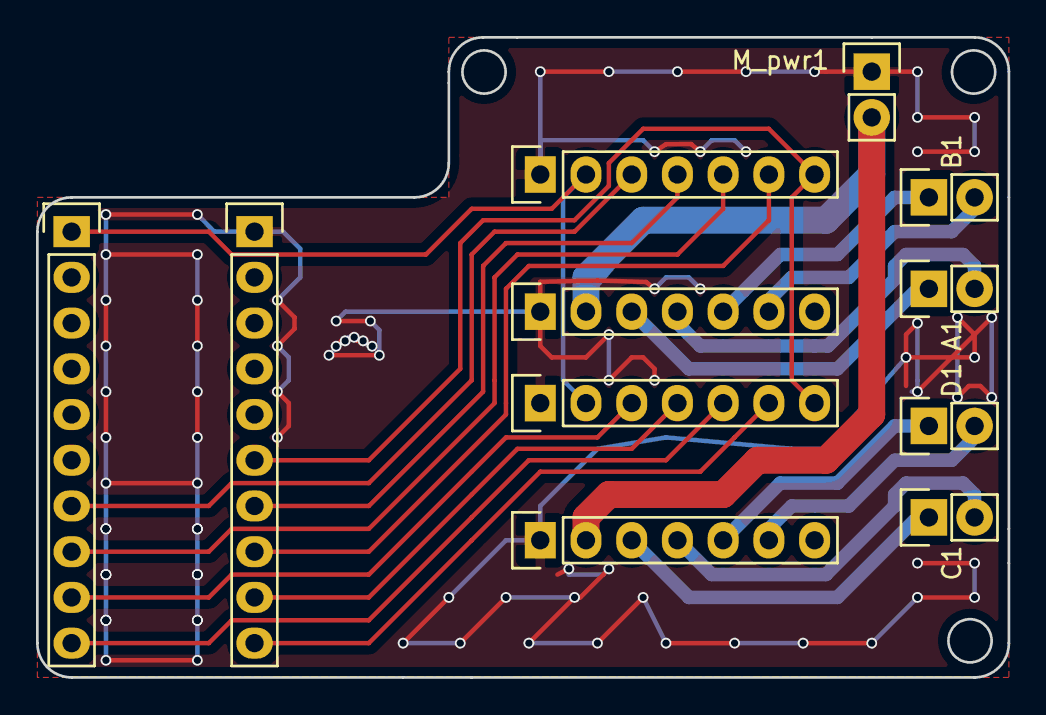
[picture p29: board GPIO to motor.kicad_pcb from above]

Board: 2 copper layers, 54.0 x 35.6 mm, 11 parts (0 on the bottom side), 20 nets.

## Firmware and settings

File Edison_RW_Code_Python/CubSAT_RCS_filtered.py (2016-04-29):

import smbus
import mraa 
import time 
import math
import numpy as np
import scipy.signal as signal
import IMU

##################################################
# initializing Variables

A_motor_velocity=B_motor_velocity=C_motor_velocity=D_motor_velocity=0
A=B=C=D=E=F=G=H=I=0
P = 0.3 # proportional control value
timer = 1
output = [A,B,C,D,E,F,G,H,I]
Pin = [14,20,0,21,36,48,47,32,46] #PWM for GP13,GP12,GP182,GP183 Gpio for GP14,GP15,GP49,GP46,GP47

######################################################
def butter_lowpass(cutoff, fs, order):
    nyq = 0.5 * fs
    normal_cutoff = cutoff / nyq
    b, a = signal.butter(order, normal_cutoff, btype='low', analog=False)
    return b, a

def manual_filt_low(b,a,data_in,data_out):
	n = len(b)-1
	#print n, data_in, b, a
	out = b[0]*data_in[n]/a[0]
	n-=1
	for x in range(n+1):
		out += b[x+1]*data_in[n]/a[0]
		out -= a[x+1]*data_out[n]/a[0]
		#print n,x+1, out, a[x+1], b[x+1]
		n-=1
	return out

def floating_array_filter(b,a,in_window,out_window,in_temp):
	in_window.append(in_temp)
	in_window.pop(0)
	out_temp = manual_filt_low(b,a,in_window,out_window)
	out_window.append(out_temp)
	out_window.pop(0)
	return out_temp, out_window, in_window
######################################################
# enabling outputs 
for x in xrange(0,4):
	output[x] = mraa.Pwm(Pin[x])
	output[x].period_us(700)
	output[x].enable(True)
	#print x, output[x]
for x in xrange(4,9):
	output[x] = mraa.Gpio(Pin[x])
	output[x].dir(mraa.DIR_OUT)
	#print x, output[x]
[Apwm,Bpwm,Cpwm,Dpwm,Adir,Bdir,Cdir,Ddir,mode] = output
output[8].write(1) #Set mode pin to high for pwm/direction

def gyroread():
        c = 0
        a = time.time()
        while c <= timer:
                [ACCx,ACCy,ACCz,GYRx,GYRy,GYRz,MAGx,MAGy,MAGz] = IMU.read()
                print "GYRx: %3.2f, GYRy: %3.2f,GYRz: %3.2f" %(GYRx,GYRy,GYRz)
                b = time.time()
                c = b - a
def A_motor_dir():
        global A_motor_speed
        if A_motor_velocity >= 0:
                 A_motor_dir = 1
                 A_motor_speed = abs(A_motor_velocity)/100
                 if A_motor_speed > 1:
                         A_motor_speed = 1
        elif A_motor_velocity < 0:
                 A_motor_dir = 0
                 A_motor_speed = abs(A_motor_velocity)/100
                 if A_motor_speed > 1:
                         A_motor_speed = 1
        Adir.write(A_motor_dir)
def B_motor_dir():
        global B_motor_speed
        if B_motor_velocity >= 0:
                 B_motor_dir = 1
                 B_motor_speed = abs(B_motor_velocity)/100
                 if B_motor_speed > 1:
                         B_motor_speed = 1
        elif B_motor_velocity < 0:
                 B_motor_dir = 0
                 B_motor_speed = abs(B_motor_velocity)/100
                 if B_motor_speed > 1:
                         B_motor_speed = 1
        Bdir.write(B_motor_dir)
def C_motor_dir():
        global C_motor_speed
        if C_motor_velocity >= 0:
                 C_motor_dir = 1
                 C_motor_speed = abs(C_motor_velocity)/100
                 if C_motor_speed > 1:
                         C_motor_speed = 1
        elif C_motor_velocity < 0:
                 C_motor_dir = 0
                 C_motor_speed = abs(C_motor_velocity)/100
                 if C_motor_speed > 1:
                         C_motor_speed = 1
        Cdir.write(C_motor_dir)
def D_motor_dir():
        global D_motor_speed
        if D_motor_velocity >= 0:
                 D_motor_dir = 1
                 D_motor_speed = abs(D_motor_velocity)/100
                 if D_motor_speed > 1:
                         D_motor_speed = 1
        elif D_motor_velocity < 0:
                 D_motor_dir = 0
                 D_motor_speed = abs(D_motor_velocity)/100
                 if D_motor_speed > 1:
                         D_motor_speed = 1
        Ddir.write(D_motor_dir)
def roll_control(in_x_window,out_x_window,in_y_window,out_y_window,in_z_window,out_z_window):
	t_a=time.time()
	
        global A_motor_velocity,B_motor_velocity,C_motor_velocity,D_motor_velocity
        global ACCx,ACCy,ACCz,GYRx,GYRy,GYRz,MAGx,MAGy,MAGz
        [ACCx,ACCy,ACCz,GYRx,GYRy,GYRz,MAGx,MAGy,MAGz] = IMU.read()
        GYRz, out_z_window, in_z_window = floating_array_filter(b,a,in_z_window,out_z_window,GYRz)
	
        A_motor_velocity = P*GYRz + A_motor_velocity
        B_motor_velocity = P*GYRz + B_motor_velocity
        C_motor_velocity = P*GYRz + C_motor_velocity
        D_motor_velocity = P*GYRz + D_motor_velocity
        
        A_motor_dir()
        B_motor_dir()
        C_motor_dir()
        D_motor_dir()
        
        Apwm.write(A_motor_speed)
        Bpwm.write(B_motor_speed)
        Cpwm.write(C_motor_speed)
        Dpwm.write(D_motor_speed)
        
order = 2
fs = 95       # sample rate, Hz
cutoff = 15    # desired cutoff frequency of the filter, Hz
b,a = butter_lowpass(cutoff, fs, order)
in_x_window = [0.0]*(len(b))
out_x_window = [0.0]*(len(a))
in_y_window = [0.0]*(len(b))
out_y_window = [0.0]*(len(a))
in_z_window = [0.0]*(len(b))
out_z_window = [0.0]*(len(a))


while True:
        roll_control(in_x_window,out_x_window,in_y_window,out_y_window,in_z_window,out_z_window)
        print "GYRz: %3.2f, A: %3.2f, B: %3.2f, C: %3.2f, D: %3.2f" %(GYRz,A_motor_velocity,B_motor_velocity,C_motor_velocity,D_motor_velocity)
       

##        print "GYRx: %3.2f, GYRy: %3.2f,GYRz: %3.2f" %(GYRx,GYRy,GYRz)
        

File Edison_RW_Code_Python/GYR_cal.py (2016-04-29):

import smbus
import time
import math
import sys
import numpy as np
import scipy.signal as signal
from LSM9DS0 import *

bus = smbus.SMBus(1)

LA_So = .000732 # g/LSB (16g)
M_GN = 0.48 # mgauss/LSB (12 gauss)
G_So = 0.00875 # dps/LSB (2000dps)
GYRx_bias = 0
GYRy_bias = 0
GYRz_bias = 0


def writeACC(register,value):
        bus.write_byte_data(ACC_ADDRESS , register, value)
        return -1

def writeMAG(register,value):
        bus.write_byte_data(MAG_ADDRESS, register, value)
        return -1

def writeGRY(register,value):
        bus.write_byte_data(GYR_ADDRESS, register, value)
        return -1

def readACCx():
        acc_l = bus.read_byte_data(ACC_ADDRESS, OUT_X_L_A)
        acc_h = bus.read_byte_data(ACC_ADDRESS, OUT_X_H_A)
	acc_combined = (acc_l | acc_h <<8)

	return acc_combined  if acc_combined < 32768 else acc_combined - 65536

def readACCy():
        acc_l = bus.read_byte_data(ACC_ADDRESS, OUT_Y_L_A)
        acc_h = bus.read_byte_data(ACC_ADDRESS, OUT_Y_H_A)
	acc_combined = (acc_l | acc_h <<8)

	return acc_combined  if acc_combined < 32768 else acc_combined - 65536

def readACCz():
        acc_l = bus.read_byte_data(ACC_ADDRESS, OUT_Z_L_A)
        acc_h = bus.read_byte_data(ACC_ADDRESS, OUT_Z_H_A)
	acc_combined = (acc_l | acc_h <<8)

	return acc_combined  if acc_combined < 32768 else acc_combined - 65536

def readMAGx():
        mag_l = bus.read_byte_data(MAG_ADDRESS, OUT_X_L_M)
        mag_h = bus.read_byte_data(MAG_ADDRESS, OUT_X_H_M)
        mag_combined = (mag_l | mag_h <<8)

        return mag_combined  if mag_combined < 32768 else mag_combined - 65536

def readMAGy():
        mag_l = bus.read_byte_data(MAG_ADDRESS, OUT_Y_L_M)
        mag_h = bus.read_byte_data(MAG_ADDRESS, OUT_Y_H_M)
        mag_combined = (mag_l | mag_h <<8)

        return mag_combined  if mag_combined < 32768 else mag_combined - 65536


def readMAGz():
        mag_l = bus.read_byte_data(MAG_ADDRESS, OUT_Z_L_M)
        mag_h = bus.read_byte_data(MAG_ADDRESS, OUT_Z_H_M)
        mag_combined = (mag_l | mag_h <<8)

        return mag_combined  if mag_combined < 32768 else mag_combined - 65536

def readGYRx():
        gyr_l = bus.read_byte_data(GYR_ADDRESS, OUT_X_L_G)
        gyr_h = bus.read_byte_data(GYR_ADDRESS, OUT_X_H_G)
        gyr_combined = (gyr_l | gyr_h <<8)

        return gyr_combined  if gyr_combined < 32768 else gyr_combined - 65536
  
def readGYRy():
        gyr_l = bus.read_byte_data(GYR_ADDRESS, OUT_Y_L_G)
        gyr_h = bus.read_byte_data(GYR_ADDRESS, OUT_Y_H_G)
        gyr_combined = (gyr_l | gyr_h <<8)

        return gyr_combined  if gyr_combined < 32768 else gyr_combined - 65536

def readGYRz():
        gyr_l = bus.read_byte_data(GYR_ADDRESS, OUT_Z_L_G)
        gyr_h = bus.read_byte_data(GYR_ADDRESS, OUT_Z_H_G)
        gyr_combined = (gyr_l | gyr_h <<8)

        return gyr_combined  if gyr_combined < 32768 else gyr_combined - 65536

	
#initialise the accelerometer
writeACC(CTRL_REG1_XM, 0b01100111) #z,y,x axis enabled, continuos update,  100Hz data rate
writeACC(CTRL_REG2_XM, 0b00100000) #+/- 16G full scale

#initialise the magnetometer
writeMAG(CTRL_REG5_XM, 0b11110000) #Temp enable, M data rate = 50Hz
writeMAG(CTRL_REG6_XM, 0b01100000) #+/-12gauss
writeMAG(CTRL_REG7_XM, 0b00000000) #Continuous-conversion mode

#initialise the gyroscope
writeGRY(CTRL_REG1_G, 0b00001111) #Normal power mode, all axes enabled (95 Hz 12.5 cutoff)
writeGRY(CTRL_REG2_G, 0b00100001) #High-pass filter: Normal mode, 13.5 Hz
writeGRY(CTRL_REG4_G, 0b00000000) #Continuos update, 245 dps full scale

start = time.time()
count = 0
while timer<15:
        t_a=time.time()
	GYRx = readGYRx()
	GYRy = readGYRy()
	GYRz = readGYRz()
	bias_totx += GYRx
	bias_toty += GYRy
	bias_totz += GYRz
	count+=1
	timer=time.time()-start
	t_b=time.time()
	t = t_b-t_a
	t_tot+=t
	print "GYRx: %2.1f, GYRy: %2.1f, GYRz: %2.1f, loop time: %2.4f" %(GYRx,GYRy,GYRz,t)
	
        
biasx = bias_totx/count
biasy = bias_toty/count
biasz = bias_totz/count
avg_t = t_tot/count
print "GYRx bias = %3.1f" % (biasx)
print "GYRy bias = %3.1f" % (biasy)
print "GYRz bias = %3.1f" % (biasz)
print "average lp time (ms) = %1.5f" % (avg_t)

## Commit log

2016-01-22 Adding work up to this point
    Includes Solidworks CAD models, Datasheets, and Board for GPIO to motor
    drivers
    [Corner rail.SLDPRT, Cube sat assembly - Corner rail-1.STL, Cube sat assembly - Corner rail-2.STL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]
2016-02-02 adding code
    CubeSAT_RCS.py is the main controller for the cubsat
    gpio_off.py is to sutdown all I/O pins
    GYR_cal.py is to determine gyro offsets
    IMU.py is the program that reads data from the IMU (this is called by
    CubeSAT_RCS.py only)
    LSM9DS0.py is a list of registers that are used by the IMU
    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
2016-02-23 Updated CAD to V2
    includes brushless motors, ESC, lipo batteries, and controller boards
    [4-40 .25 button head screw.SLDPRT, 4-40 .25 flat head screw.SLDPRT, 4-40 .25in standoff.SLDPRT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]
2016-02-23 modified the reaction wheel to add extra clearance
    and did a simple FEA of the wheel rotating at 22,000 RPM
    [Cube sat assembly.SLDASM, Motor rotational inertia.SLDASM, Motor with mass.SLDASM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]
2016-02-23 adding circuit board for GPIO to motor speed controller, and cubesat model made with octave
    [Edison_Motor_Servo.kicad_pcb, Edison_Motor_Servo.sch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]
2016-02-27 replotted gerbers for servo board
    [Edison_Motor_Servo-Edge.Cuts.gbr, Edison_Motor_Servo-F.Cu.gbr, Edison_Motor_Servo-F.Mask.gbr]
2016-02-27 I forgot to measure the header spacing :(
    [Edison_Motor_Servo-Edge.Cuts.gbr, Edison_Motor_Servo-F.Cu.gbr, Edison_Motor_Servo-F.Mask.gbr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]
2016-02-27 try again
    [Edison_Motor_Servo-Edge.Cuts.gbr, Edison_Motor_Servo-F.Cu.gbr, Edison_Motor_Servo-F.Mask.gbr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]
2016-03-14 updated open-loop system model, added screenshot of motor response graph
    [Edison_Motor_Servo.kicad_pcb]
2016-03-31 refining model
    [Hall_BLDC_controller.kicad_pcb, Hall_BLDC_controller.sch]
2016-04-26 Updated dynamics model of the cubesat reaction wheel system. Model includes a PIcontroller that is untuned
2016-04-29 Adding Drop test data, updating cube code to latest versions and adding drop test code
    [CubeSat_Drop2000-01-01_00:01:35.csv, CubeSat_Drop2000-01-01_00:26:41.csv, CubeSat_Drop2000-01-01_00:26:52.csv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]
2016-05-04 Analysis of Drop test on 4-26 and comparison to model
    [CubeSat_Drop2000-01-01_01:01:45.ods, CubeSat_Drop2000-01-01_01:21:54.csv, CubeSat_Drop2000-01-01_01:21:54.ods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]
2016-05-25 renamed files that hate windows
    [CubeSat_Drop2000-01-01_00-01-35.csv, CubeSat_Drop2000-01-01_00-26-41.csv, CubeSat_Drop2000-01-01_00-26-52.csv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]
2016-05-25 adding bode analysis drop test code
    [CubeSat_Drop2000-01-01_00:01:35.csv, CubeSat_Drop2000-01-01_00:26:41.csv, CubeSat_Drop2000-01-01_00:26:52.csv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]
2016-06-08 fixed drop test code for bode analysis.
    [Drop_Test_Bode.py]
